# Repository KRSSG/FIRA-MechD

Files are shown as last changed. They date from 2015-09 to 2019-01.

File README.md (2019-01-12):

# FIRA-MechD
Repository for the Mechanical Design of robots by IIT Kharagpur KRSSG for FIRA Roboworld Cup.

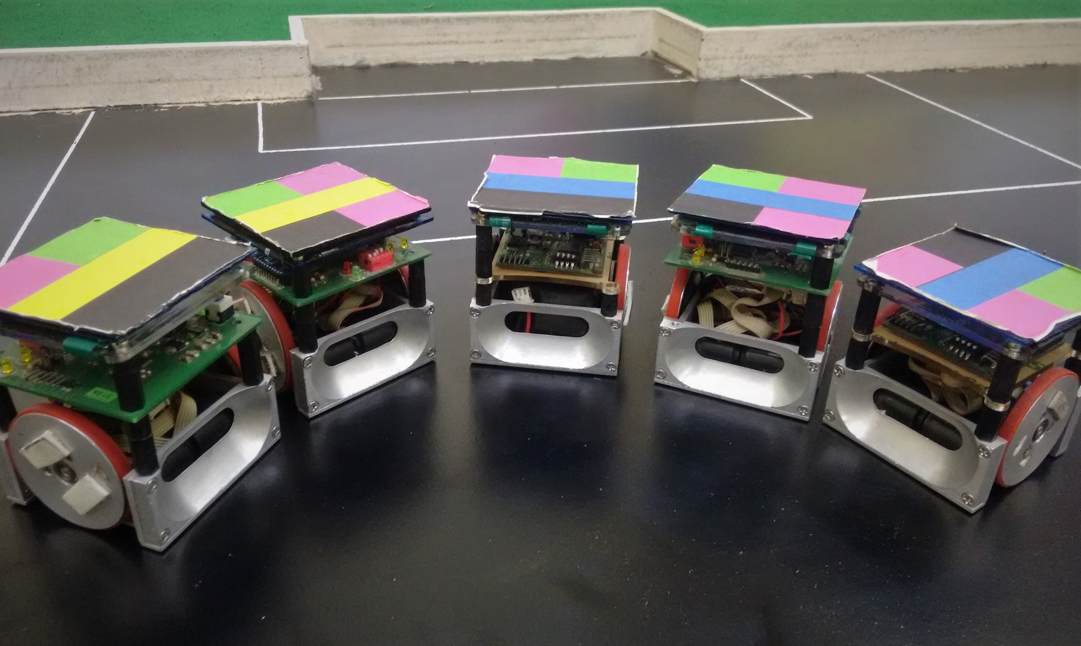
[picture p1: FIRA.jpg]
FIRA Robot Developed by KRSSG


## FIRA v1.0

### Locomotion System
The bot has two wheels parallel to each other for forward and backward movement. There are two castor wheels on the perpendicular sides of the wheel so that chassis is not in direct contact of ground as it will increase the friction.
##### Motor
The motor used is Faulhaber which is used to drive both the wheels.
##### Gear
Two spur gears,one for motor and other attached to wheel are used.
##### Wheels
Wheels are 40 mm in diameter and a rubber grip is fixed on the wheel for better friction.
Wheel-Motor Connection
The motor is mounted on chassis and then a gear is fit from outside. The wheel with gear is mounted on axle so that both the gear meshes with each other.

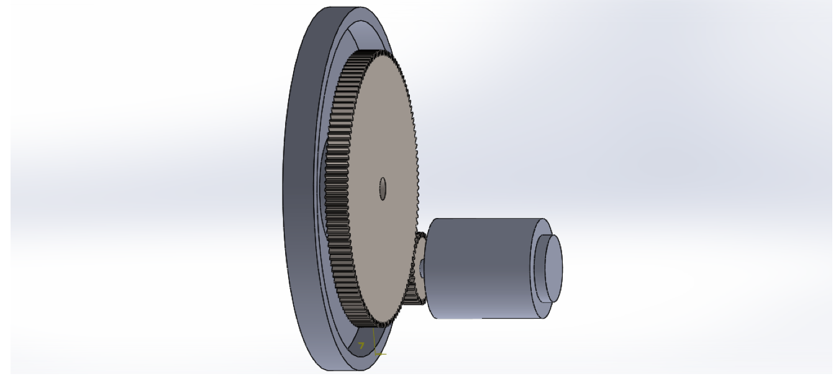
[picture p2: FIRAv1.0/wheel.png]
Wheel-Gear Assembly


### Dribbling System

The bot is not having any particular dribbling device but we make grooves in the front and back part of chassis to hold the ball while moving.it has  two groves on each side in such a way that only 20% of the ball is inside the chassis of bot.

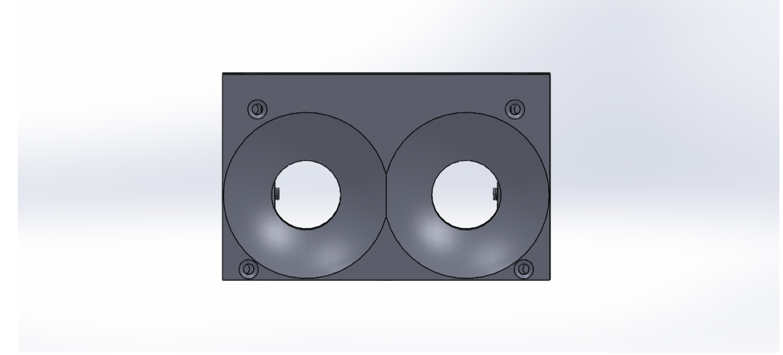
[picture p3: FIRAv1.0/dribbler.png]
Dribbler


### Chassis
Chassis is 7.5cm x 7.5cm x 6cm made up of aluminium .It is made in four different parts , two parts of wheel and two for dribbling grooves , they are joined together , mounting motor inside and mounting axle and then battery is kept over the motors in between the four sides. The motors are aligned one after other .Then circuit is mounted at the top of the chassis with the help of studs.

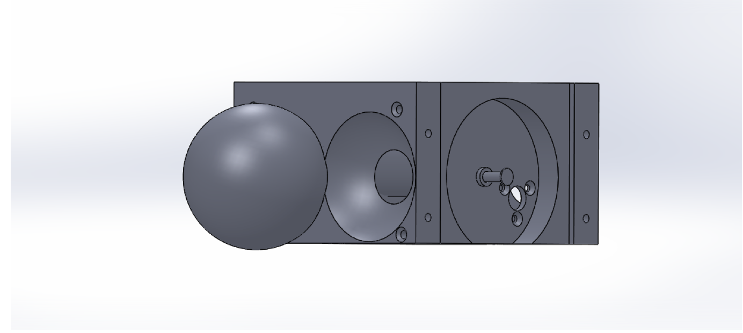
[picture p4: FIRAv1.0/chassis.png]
Chassis


## FIRA v2.0

There is not much difference in overall chassis of the robot excpet for two major changes:

#### Dribbling System
The front two grooves have been merged into a single groove for better control over the ball.

#### Caster Ball
The assembly of the two caster balls have been improved. An additional plate at the bottom now supports the balls in their grooves.

FIRA v2.0 Assembly

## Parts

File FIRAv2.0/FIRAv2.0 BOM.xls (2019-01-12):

ITEM NO. | PART NUMBER | QTY. | MATERIAL | DESCRIPTION
1 | Base | 1 | Aluminium 6061
2 | Front plate | 2 | Aluminium 6061
3 | Side plate | 2 | Aluminium 6061
4 | Wheel | 2 | Aluminium 6061
5 | Washer | 2 | Plain Carbon Steel
6 | Rubber ring | 2
7 | Stud/Standoff | 8 | Nylon / Steel | 15 mm, Hex Male Type
8 | Marker | 1 | Acrylic (PMMA)
9 | Marker Support | 1 | Acrylic (PMMA)
10 | Motor | 2 |  | Faulhaber Motor
11 | Battery | 1 |  | LiPo 2S
12 | Circuit Support | 1 | Acrylic (PMMA)
13 | Circuit_NRF | 1 |  | Custom PBC circuit
14 | Caster ball | 2 | Plain Carbon Steel
15 | Wheel Spur gear | 2 | Plain Carbon Steel | Module - 0.3, Teeth - 118, Face width - 2 , Pressure angle - 20 deg
16 | Screw - M3 x 0.5 x 10 | 8 |  | Countersunk, Flat Head
17 | Screw - M2.5 x 0.45 x 6 | 2 |  | Countersunk, Flat Head
18 | Screw - M2 x 0.4 x 6 | 16 |  | Countersunk, Flat Head
19 | Screw - M3 x 0.5 x 10 | 4 |  | Countersunk, Pan Head
20 | Radial Ball Bearing | 4 |  | SKF W 627/6-2Z, (AFBMA 20.1 - 27-6 - 16,SI,NC,16_68)

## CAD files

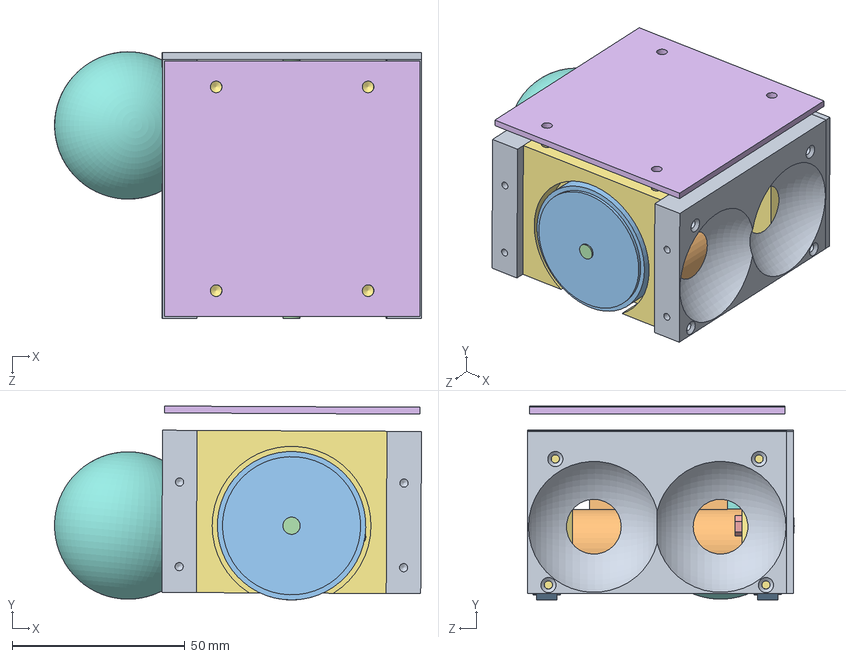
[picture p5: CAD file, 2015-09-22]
FIRAv1.0/miro2.SLDASM
106.3 x 56.2 x 77.2 mm
1 - Copy x 2
motor x 2
wheel
rod x 2
bolt x 2
new wheel cover x 2
ball
side support
battery

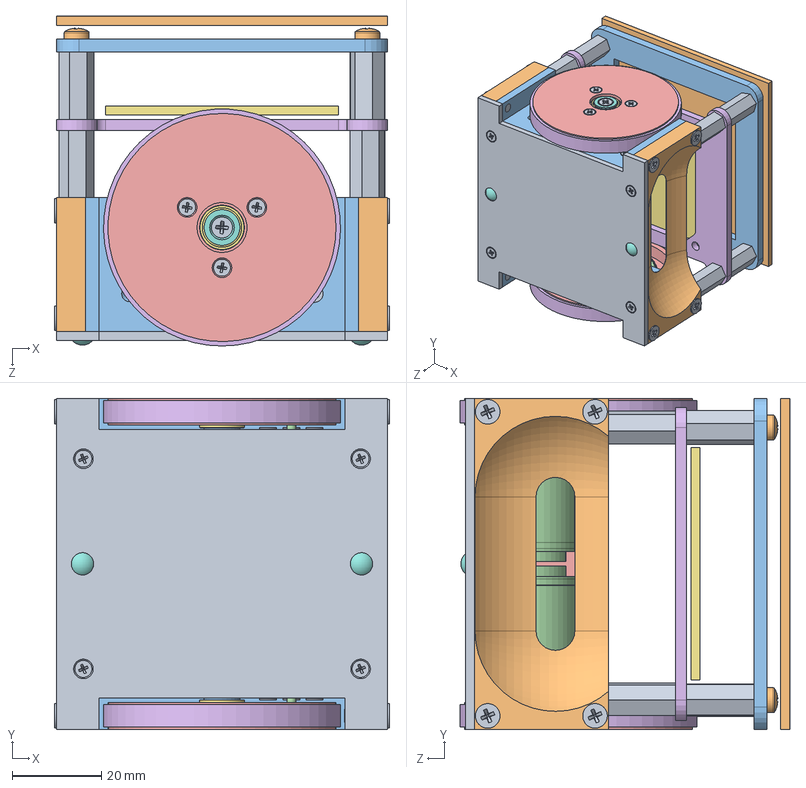
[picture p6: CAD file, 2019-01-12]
FIRAv2.0/FIRA assembly.SLDASM
75.0 x 74.1 x 73.8 mm
base
Front plate x 2
side plate x 2
Spur Gear Wheel x 2
wheel x 2
rubber ring x 2
radial ball bearing_68_am x 4
washer x 2
stud x 8
marker
Marker Support
motor x 2
battery
Circuit Support
Circuit_NRF
Caster ball x 2
flat head screw_am x 26
pan cross head_am x 4

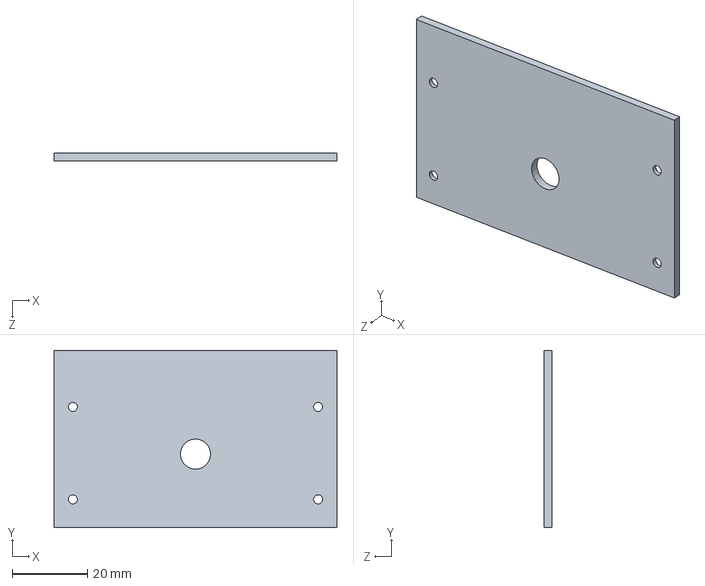
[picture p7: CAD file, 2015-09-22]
FIRAv1.0/side support.SLDPRT
75.0 x 47.0 x 2.00 mm

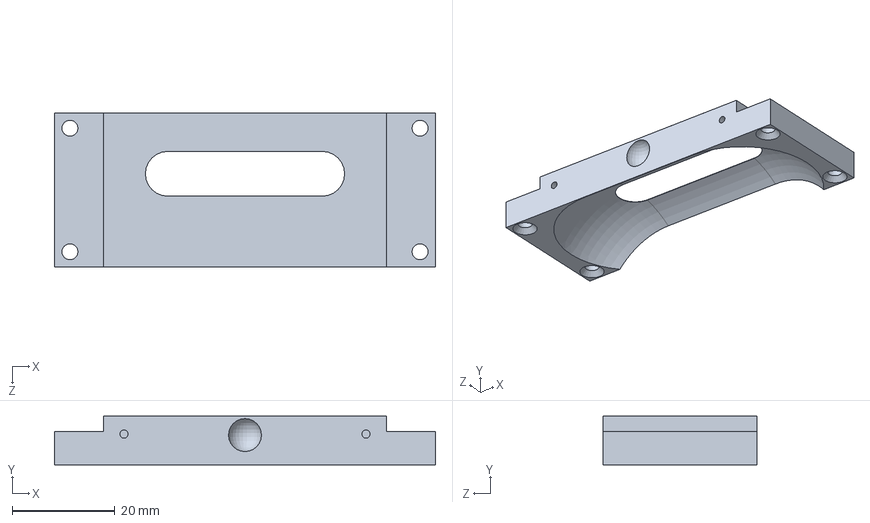
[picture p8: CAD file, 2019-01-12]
FIRAv2.0/Front plate.SLDPRT
74.0 x 9.50 x 30.0 mm

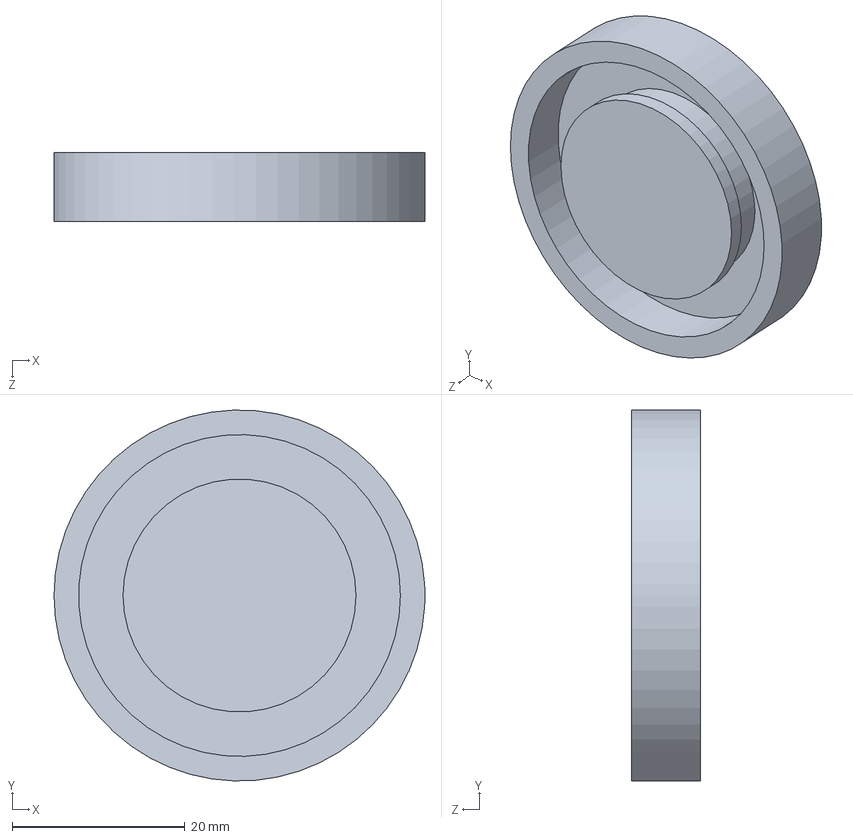
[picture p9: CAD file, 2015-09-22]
FIRAv1.0/wheel.SLDPRT
43.0 x 43.0 x 8.00 mm

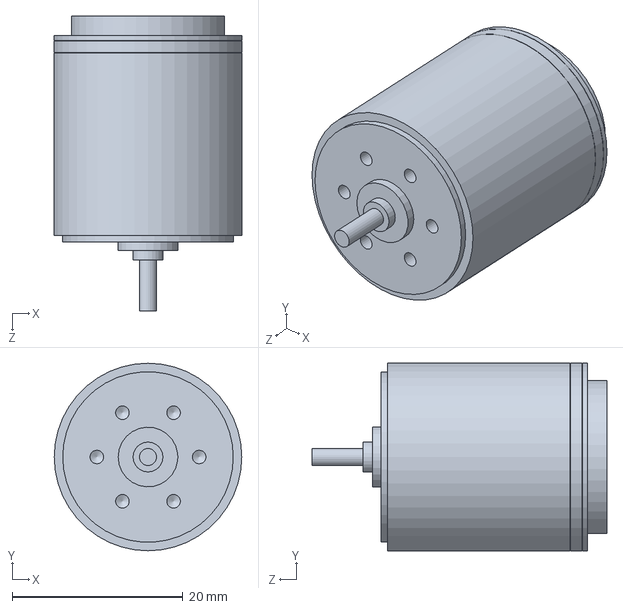
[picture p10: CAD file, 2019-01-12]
FIRAv2.0/motor.SLDPRT
22.0 x 22.0 x 34.6 mm

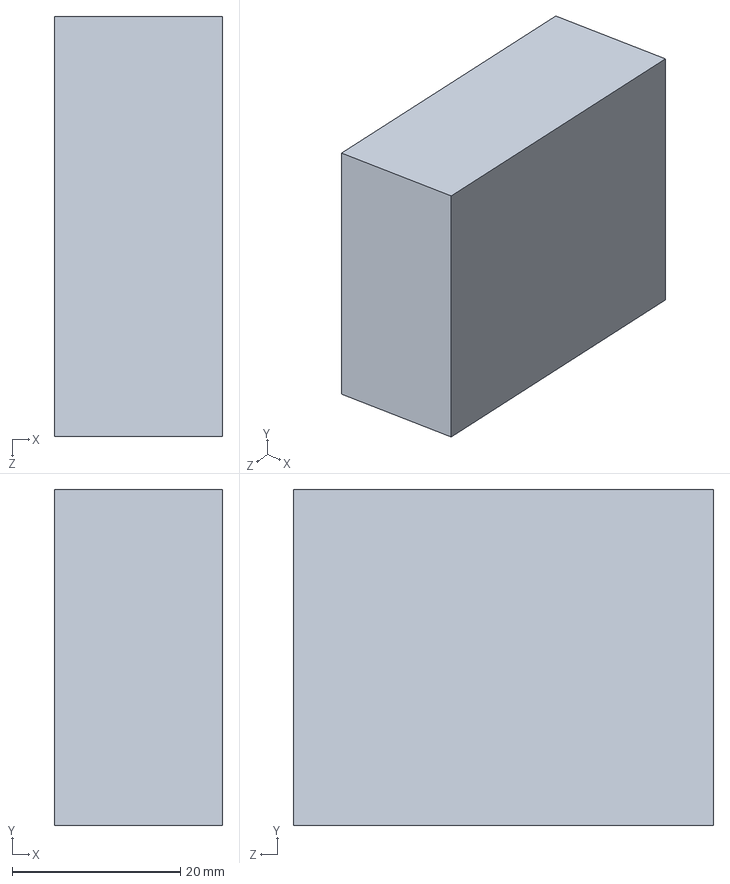
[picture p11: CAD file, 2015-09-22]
FIRAv1.0/battery.SLDPRT
20.0 x 40.0 x 50.0 mm

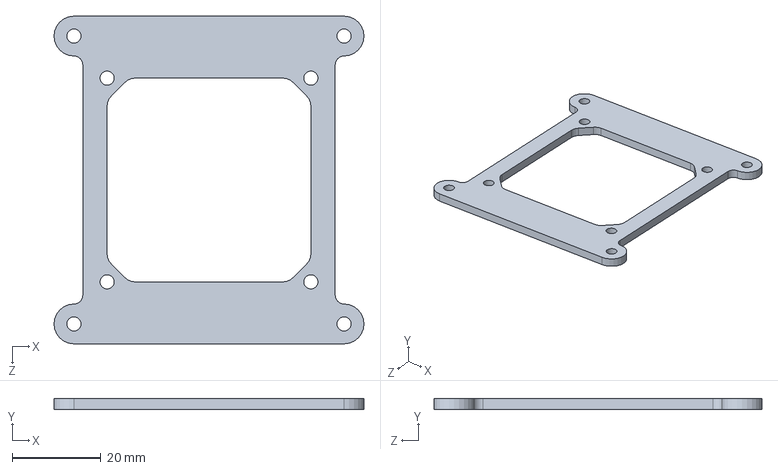
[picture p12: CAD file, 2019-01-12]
FIRAv2.0/Circuit Support.SLDPRT
70.0 x 2.50 x 74.0 mm

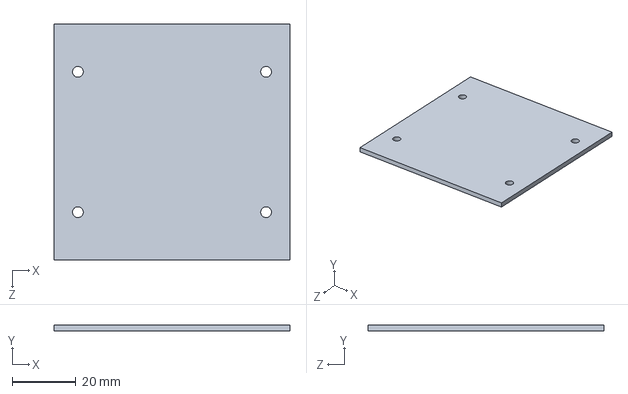
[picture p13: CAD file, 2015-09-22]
FIRAv1.0/circuit.SLDPRT
74.0 x 2.00 x 74.0 mm

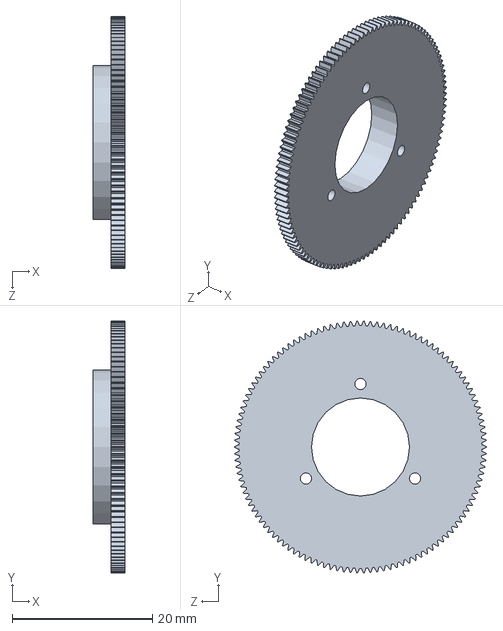
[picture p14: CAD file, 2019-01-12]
FIRAv2.0/Spur Gear Wheel.SLDPRT
4.50 x 36.0 x 36.0 mm

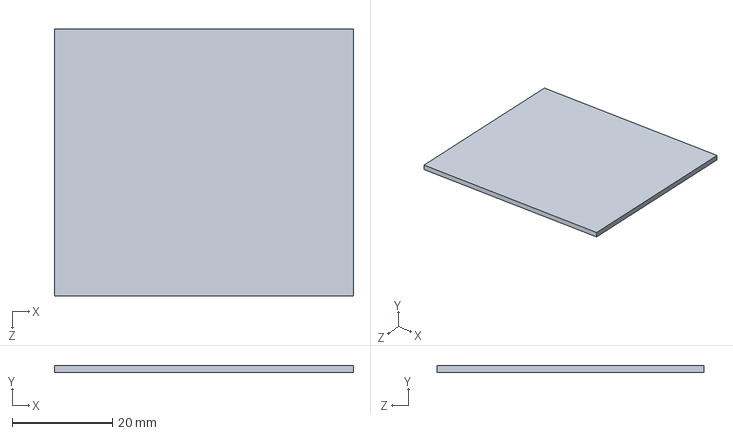
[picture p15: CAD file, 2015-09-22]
FIRAv1.0/base.SLDPRT
59.7 x 1.40 x 53.3 mm

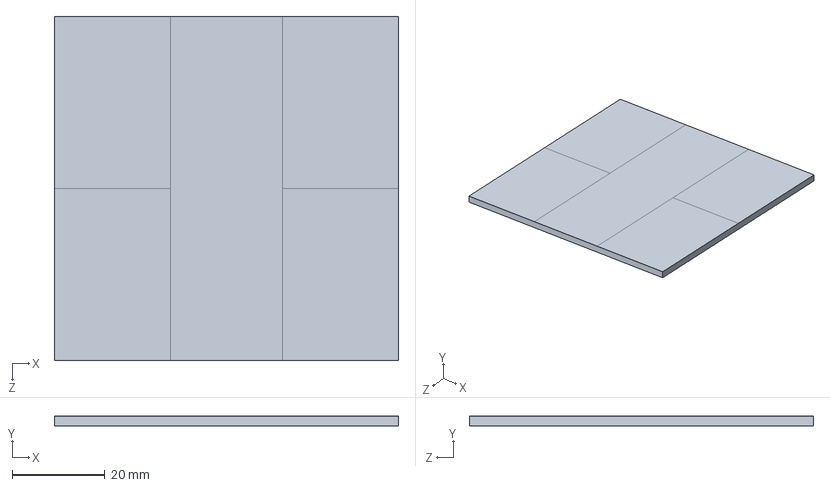
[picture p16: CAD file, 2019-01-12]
FIRAv2.0/marker.SLDPRT
74.0 x 2.10 x 74.0 mm

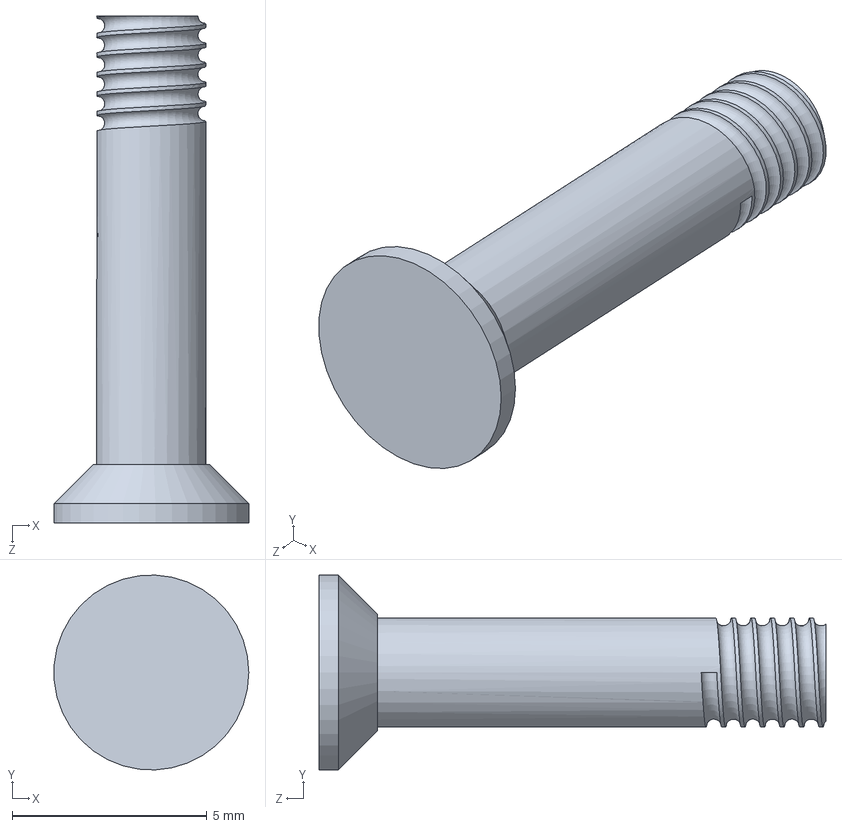
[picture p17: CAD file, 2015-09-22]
FIRAv1.0/rod.SLDPRT
4.99 x 5.00 x 13.0 mm

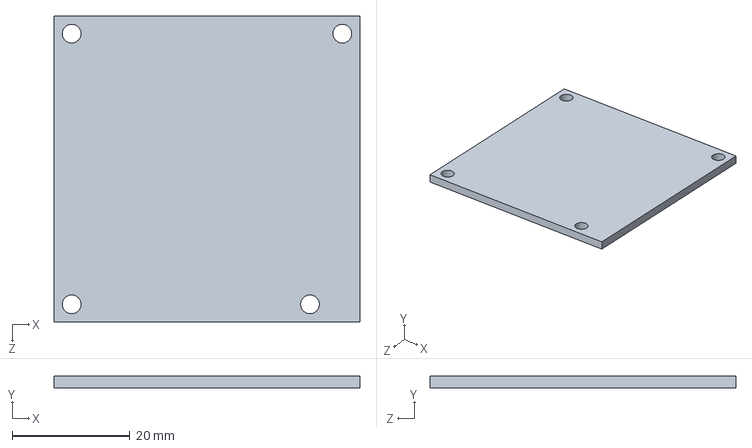
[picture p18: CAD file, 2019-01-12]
FIRAv2.0/Circuit_NRF.SLDPRT
52.0 x 2.00 x 52.0 mm

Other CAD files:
FIRAv2.0/FIRAv2.0 Assembly.STEP
FIRAv1.0/new wheel cover.SLDPRT
FIRAv2.0/stud.SLDPRT
FIRAv1.0/motor.SLDPRT
FIRAv1.0/ball.SLDPRT
FIRAv1.0/bolt.SLDPRT
FIRAv2.0/Caster ball.SLDPRT
FIRAv2.0/Marker Support.SLDPRT
FIRAv2.0/base.SLDPRT
FIRAv2.0/battery.SLDPRT
FIRAv2.0/rubber ring.SLDPRT
FIRAv2.0/side plate.SLDPRT
FIRAv2.0/washer.SLDPRT
FIRAv2.0/wheel.SLDPRT

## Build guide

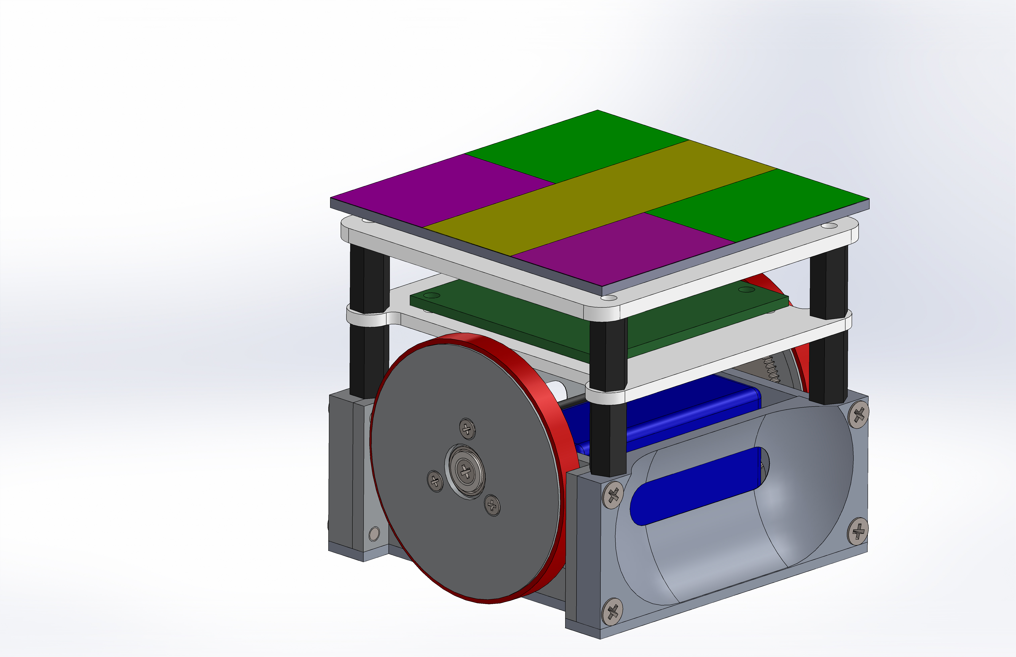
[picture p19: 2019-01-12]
FIRAv2.0/FIRA_ assembly.JPG

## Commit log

2015-09-17 FIRA v2 Added
    [FIRA assembly.SLDASM, Front plate.SLDPRT, base.SLDPRT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]
2015-09-22 SLD Parts added
    [ball.SLDPRT, base.SLDPRT, battery.SLDPRT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]
2019-01-09 CAD model updated and BOM added
    [Caster ball.SLDPRT, Circuit Support.SLDPRT, Circuit_NRF.SLDPRT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]
2019-01-09 CAD updated and BOM Added
